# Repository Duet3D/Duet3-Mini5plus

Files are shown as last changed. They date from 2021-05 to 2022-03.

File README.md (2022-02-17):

# Duet3-Mini5+
The Duet 3 Mini 5+ balances value and performance, focused on small and medium size machines that do not need the high power output of the Duet 3 Mainboard 6HC. 

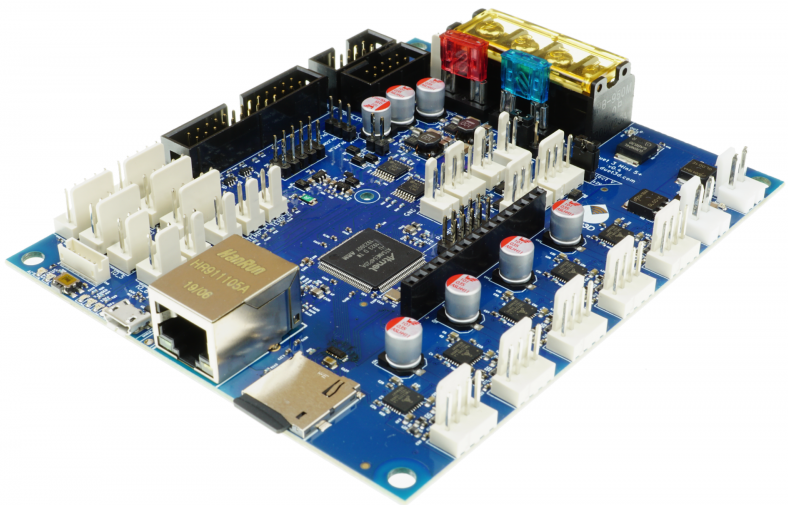
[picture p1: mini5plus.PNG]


Product page is here: https://www.duet3d.com/Duet3Mini5plus

Documentation is here: https://docs.duet3d.com/Duet3D_hardware/Duet_3_family/Duet_3_Mini_5+_Hardware_Overview

This repository also contains information in the Mini 2+ : a two driver expansion board for the Duet 3 mini 5+
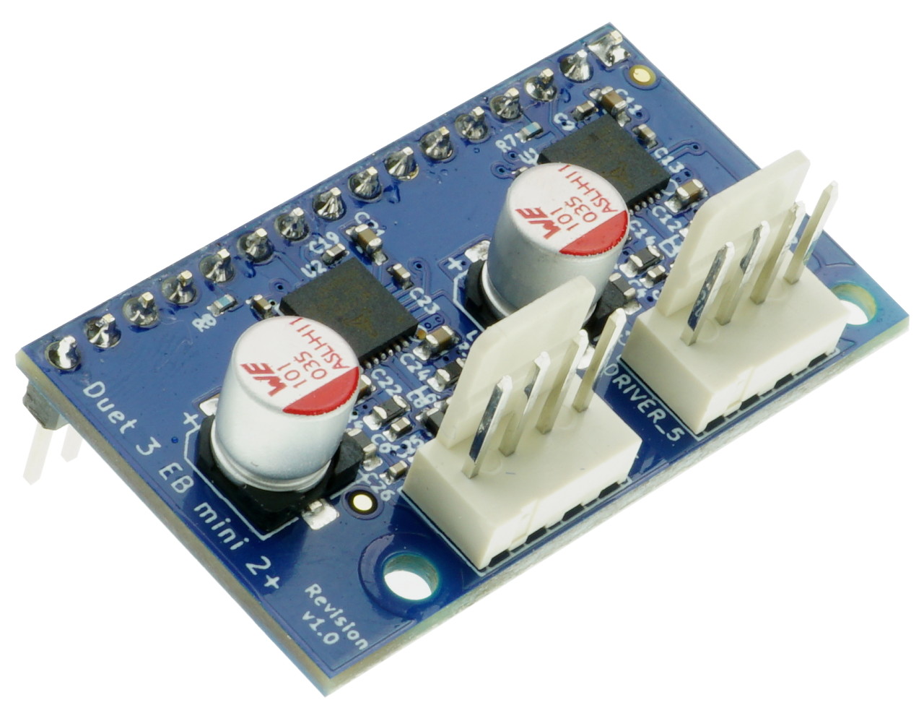
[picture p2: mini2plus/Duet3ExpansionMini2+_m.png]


Product page is here: https://www.duet3d.com/Duet3ExpansionMini2plus

Documentation is here: https://docs.duet3d.com/Duet3D_hardware/Duet_3_family/Duet_3_Expansion_Mini_2+

As always please discuss this on the Duet3d forum: https://forum.duet3d.com/

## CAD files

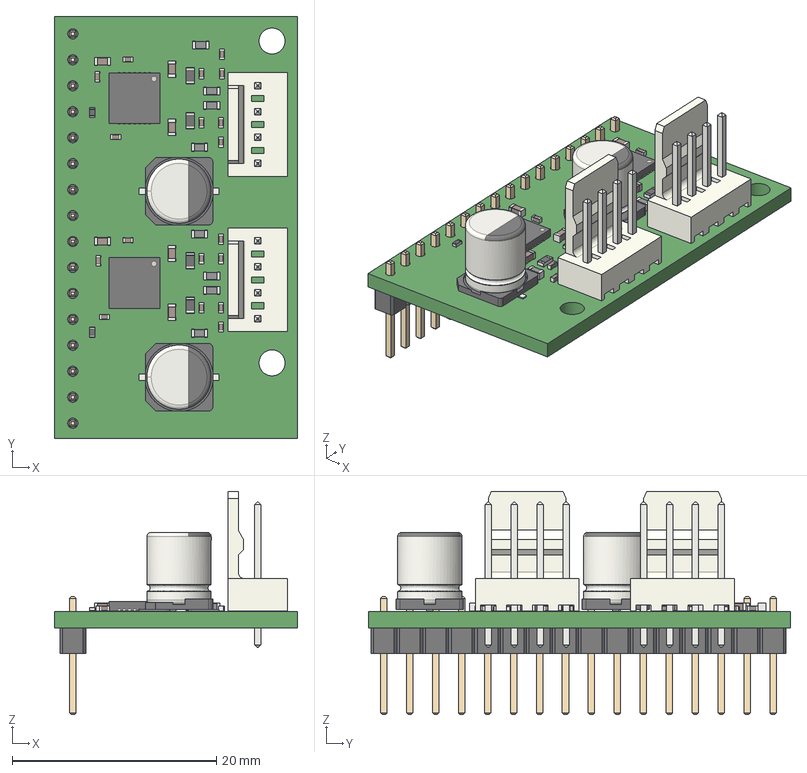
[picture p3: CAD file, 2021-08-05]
mini2plus/v1.0/Duet3_Exp_2plus.step
23.8 x 41.3 x 21.8 mm

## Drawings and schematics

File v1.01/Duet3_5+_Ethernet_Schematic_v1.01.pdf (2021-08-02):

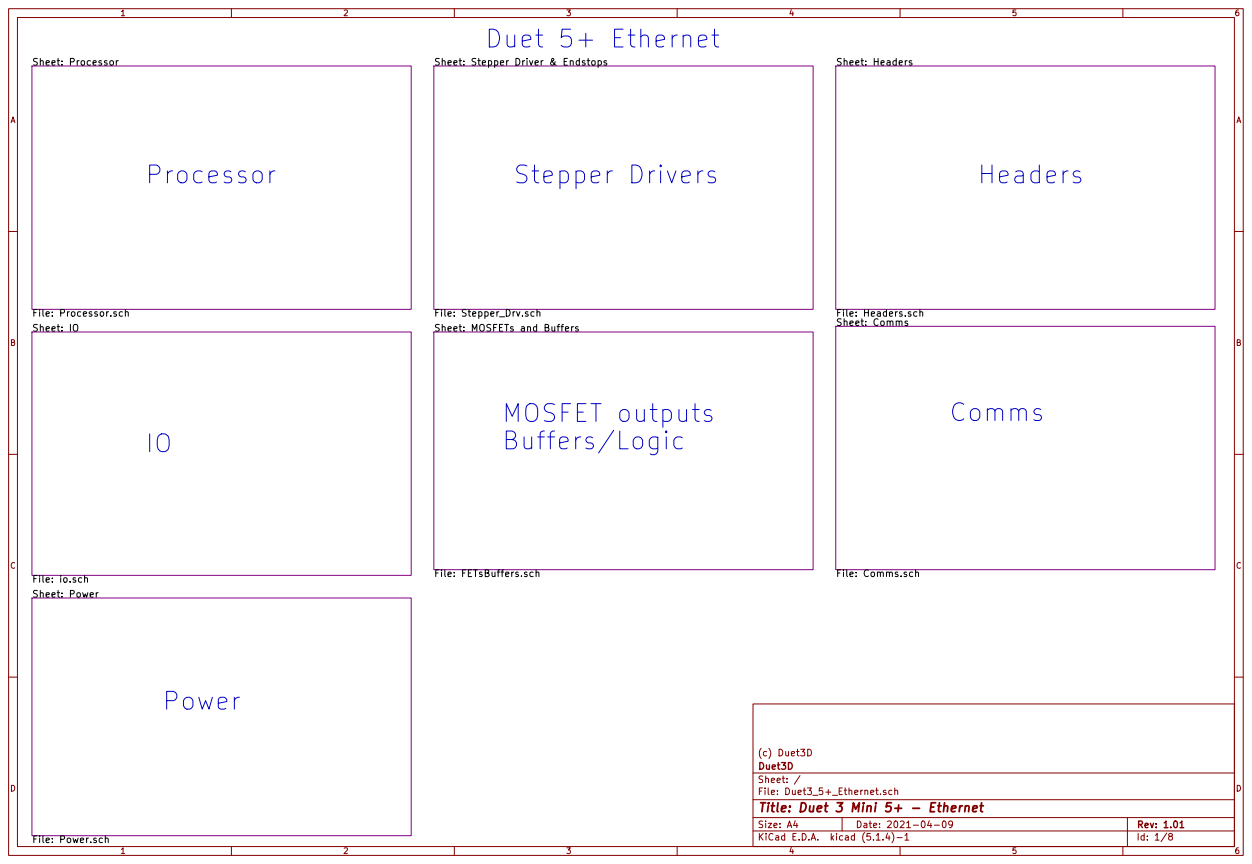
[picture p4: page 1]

Sheet: Headers File: Headers.sch Sheet: Power File: Power.sch

Sheet: Stepper Driver & Endstops

Id: 1/8 Title: Duet 3 Mini 5+ - Ethernet

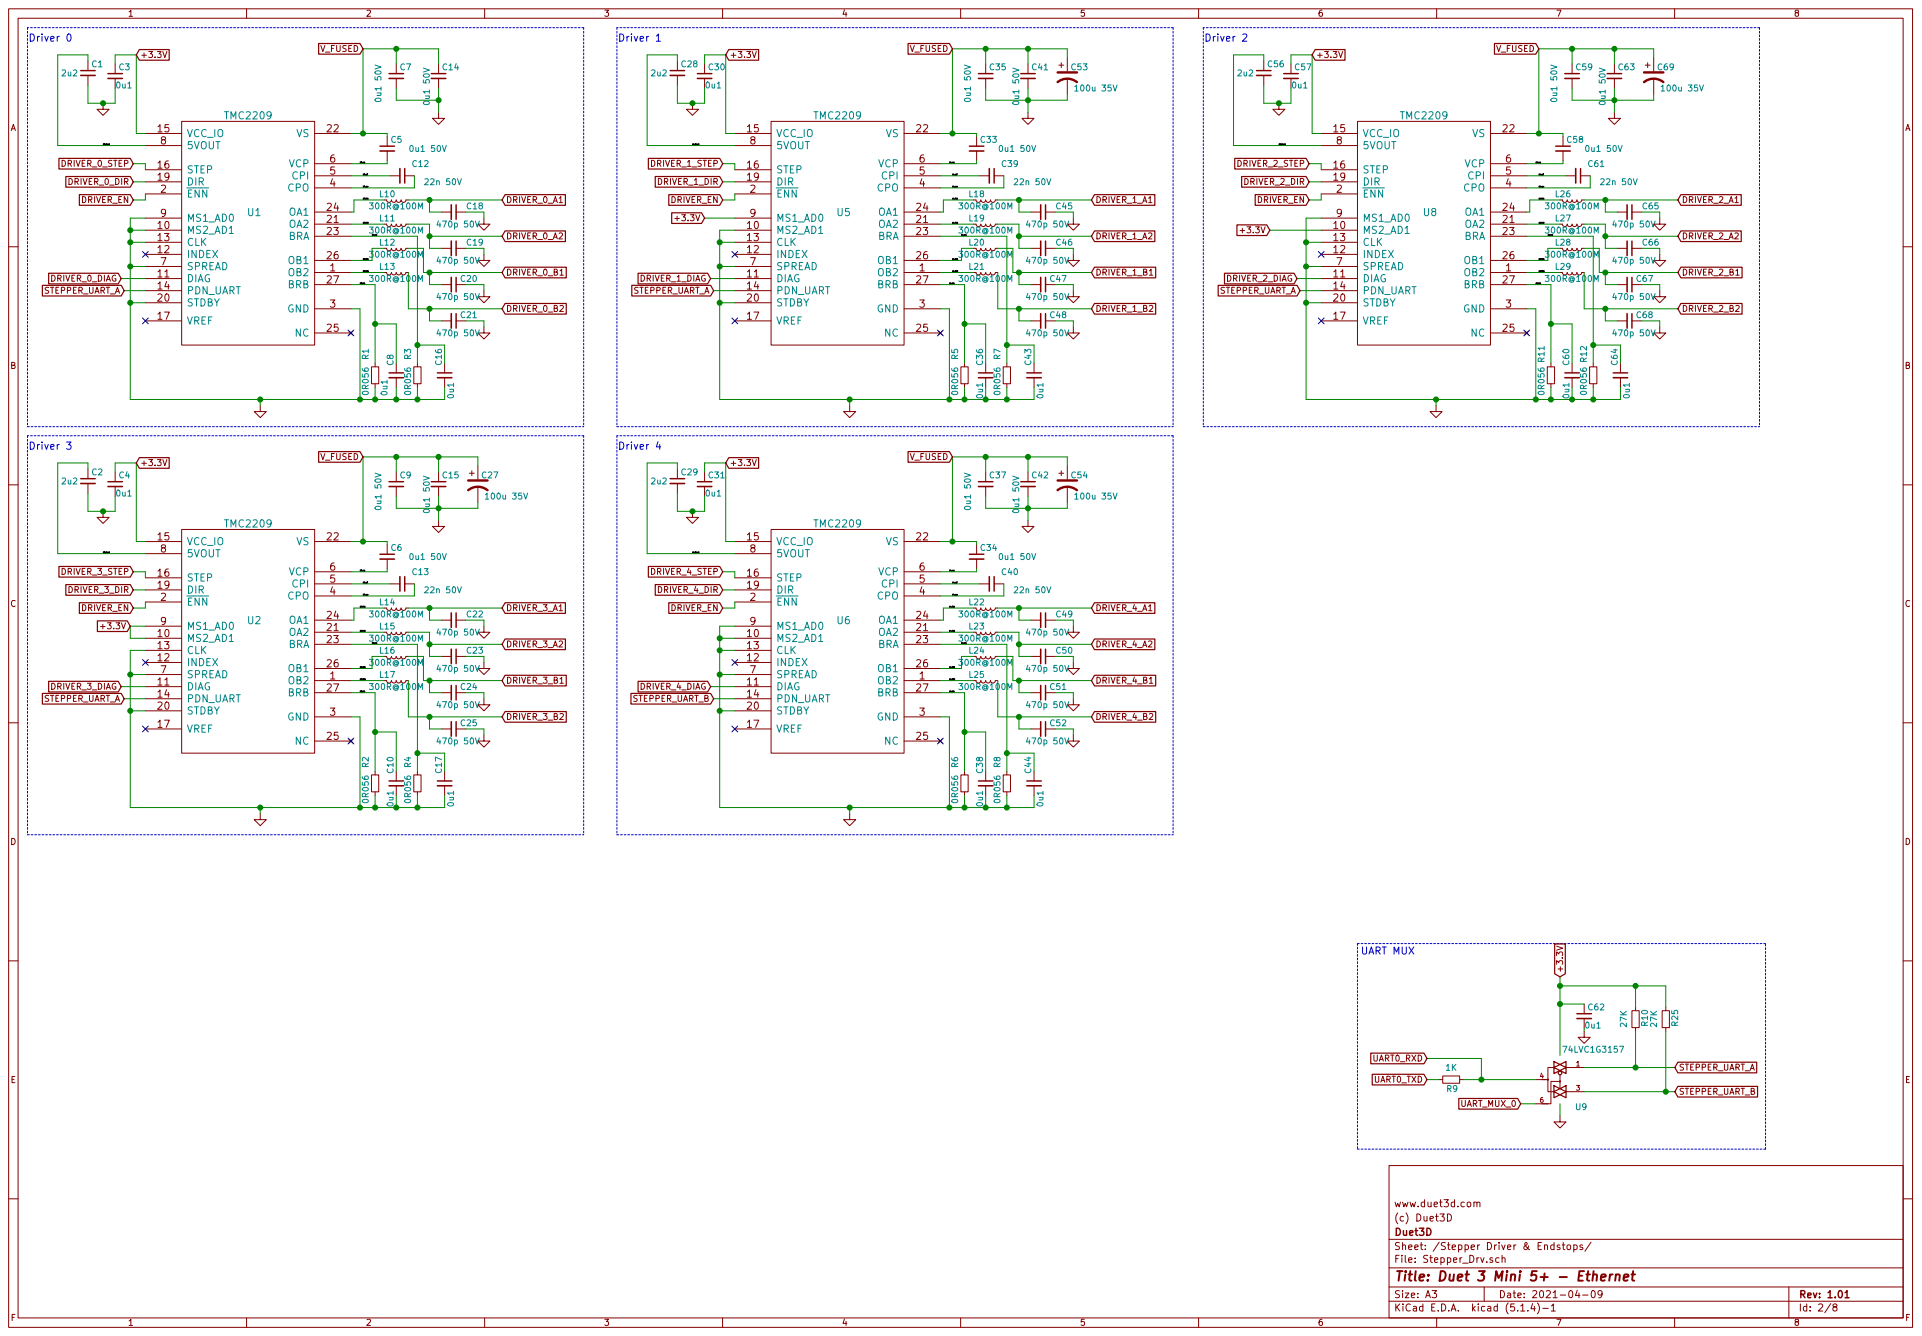
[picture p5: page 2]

www.duet3d.com
(c) Duet3D
Sheet: /Stepper Driver & Endstops/ Duet3D

File: Stepper_Drv.sch
Id: 2/8 Title: Duet 3 Mini 5+ - Ethernet

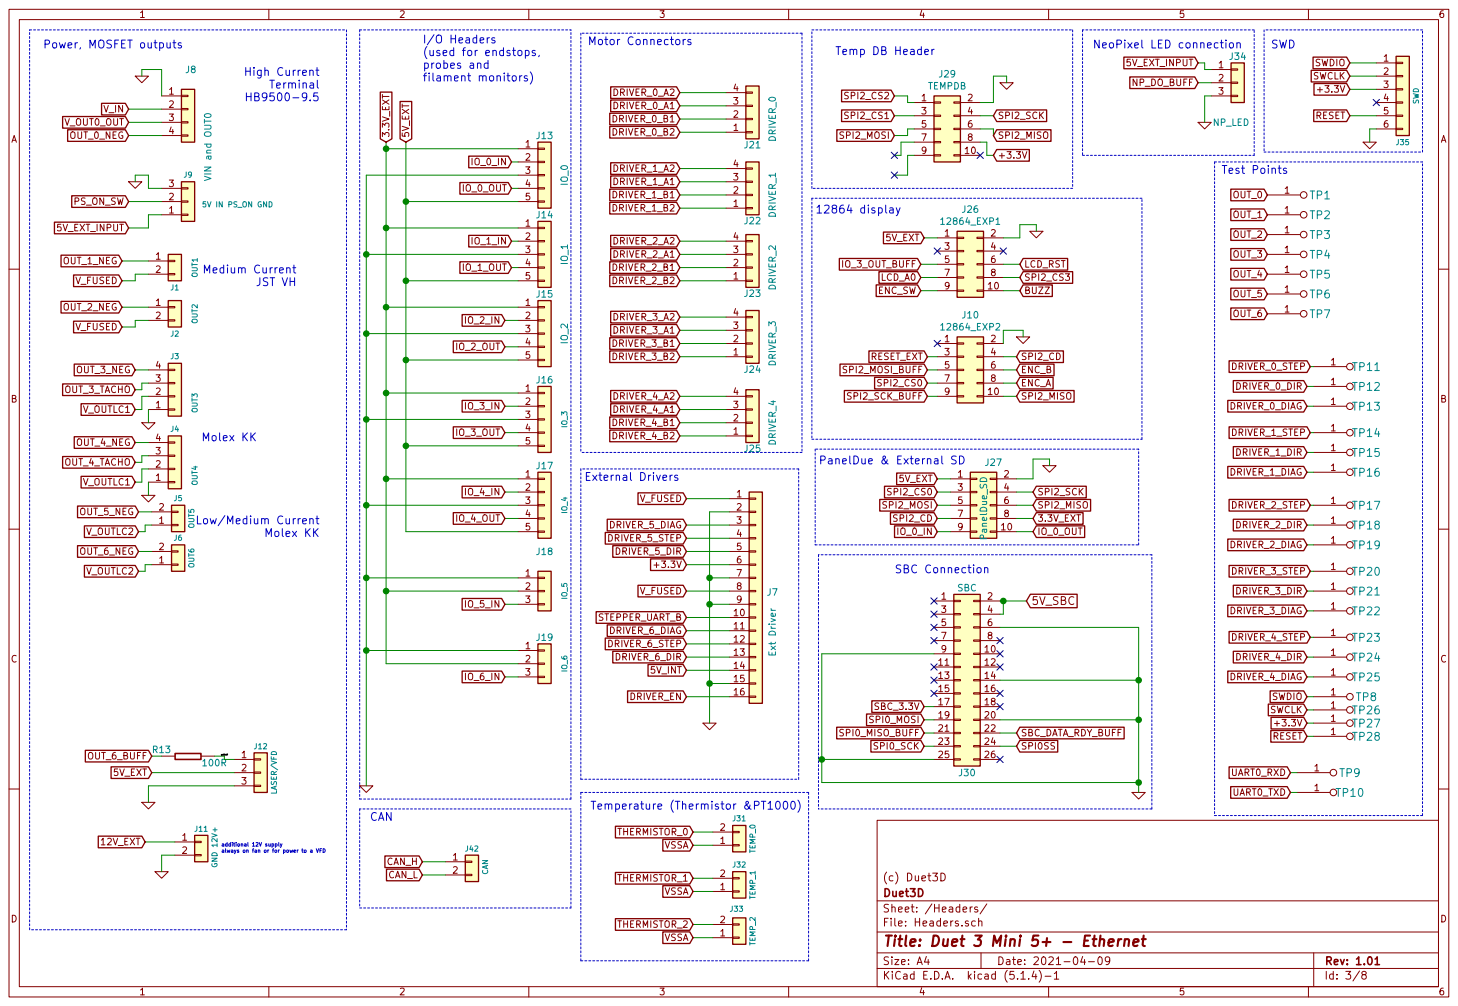
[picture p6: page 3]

High Current Terminal HB9500-9.5 Power, MOSFET outputs

4 IO_0_OUT 5

Low/Medium Current Molex KK

(c) Duet3D
Id: 3/8 Title: Duet 3 Mini 5+ - Ethernet File: Headers.sch Sheet: /Headers/ Duet3D

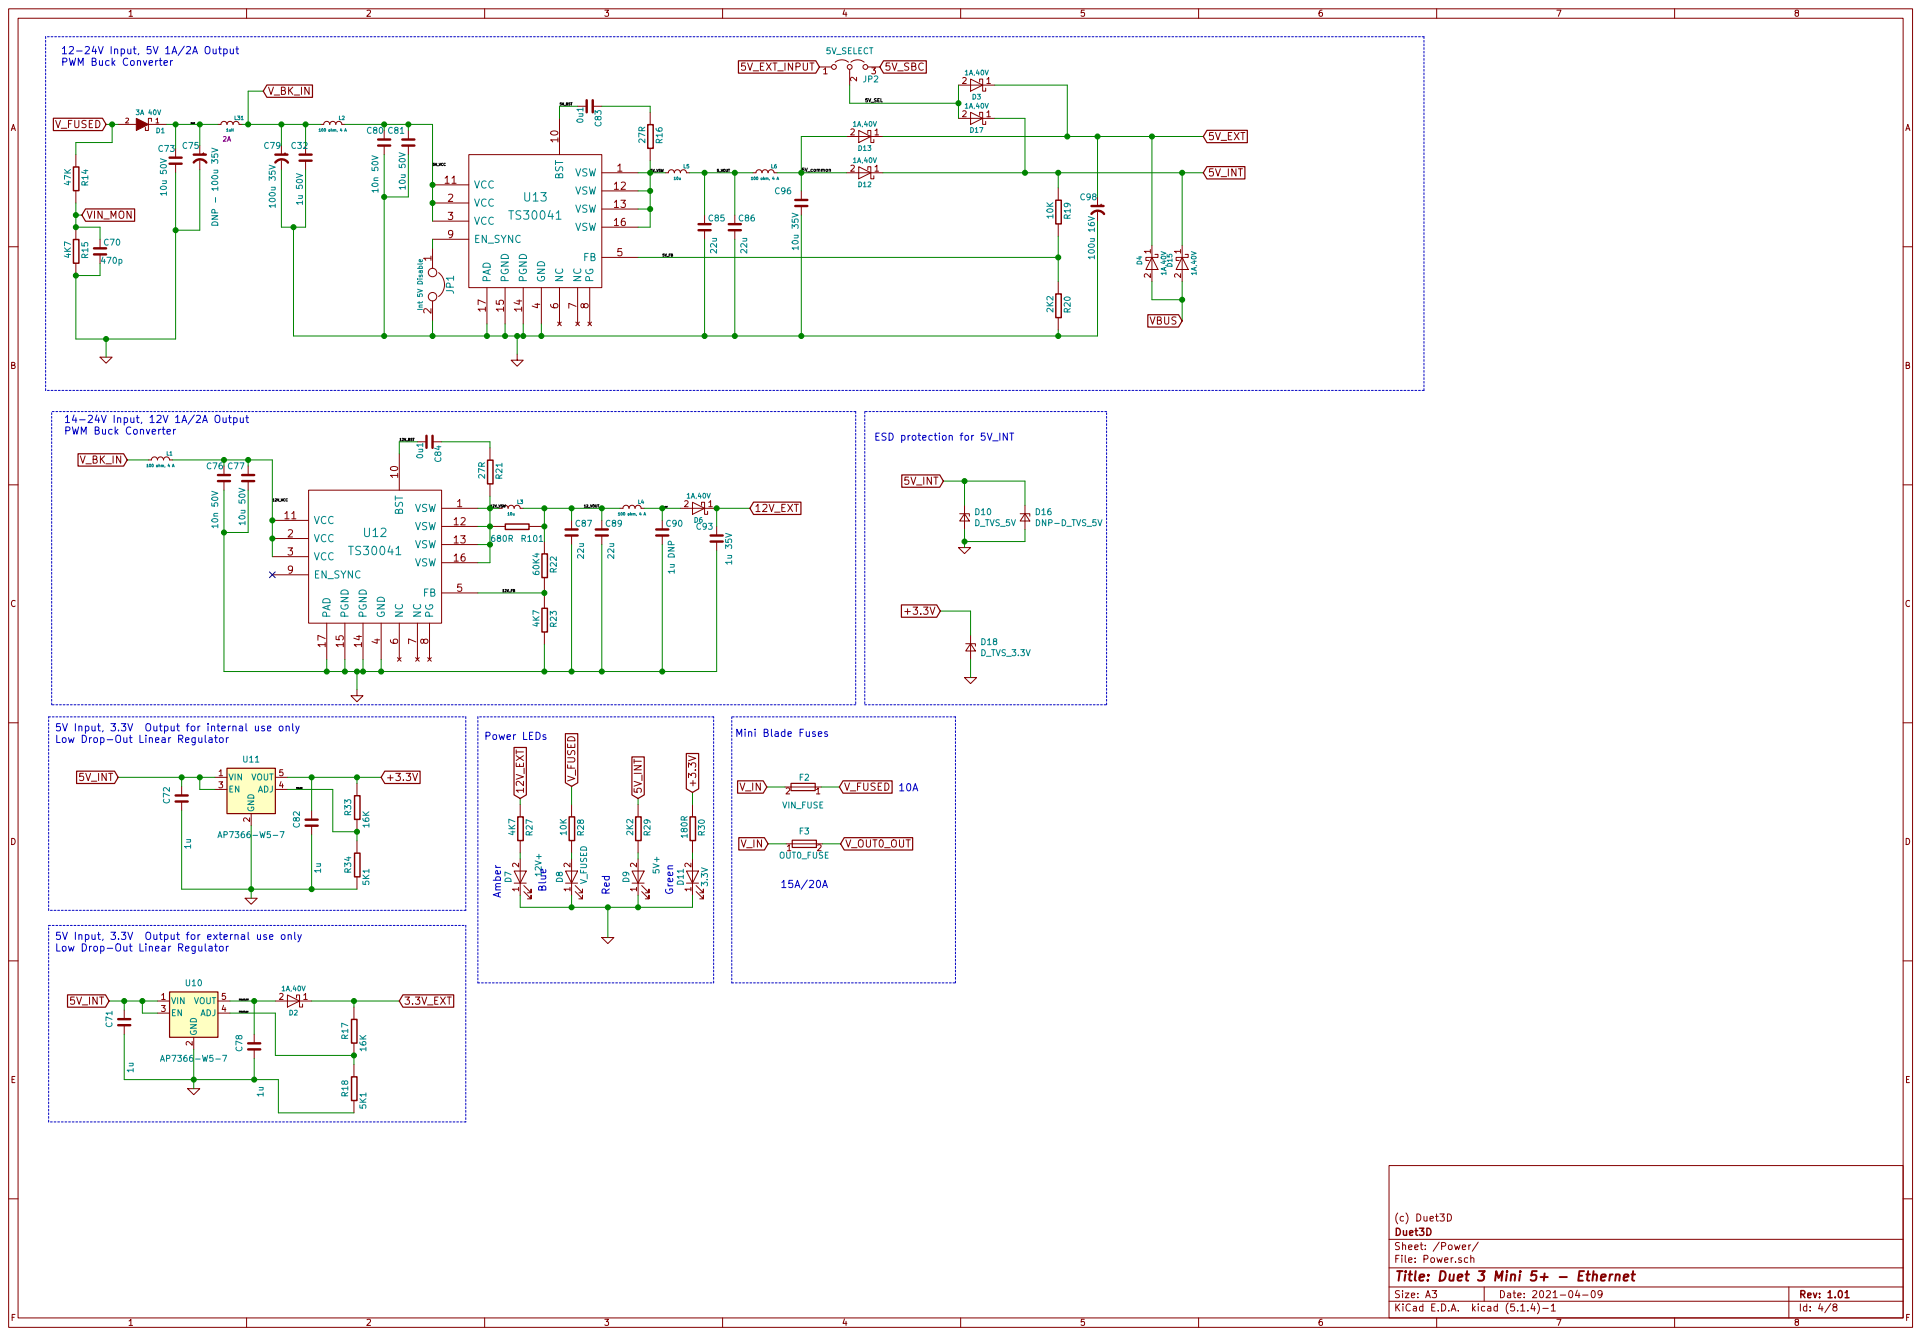
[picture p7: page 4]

5V Input, 3.3V Output for internal use only

5V Input, 3.3V Output for external use only

(c) Duet3D
Id: 4/8 Title: Duet 3 Mini 5+ - Ethernet File: Power.sch Sheet: /Power/ Duet3D

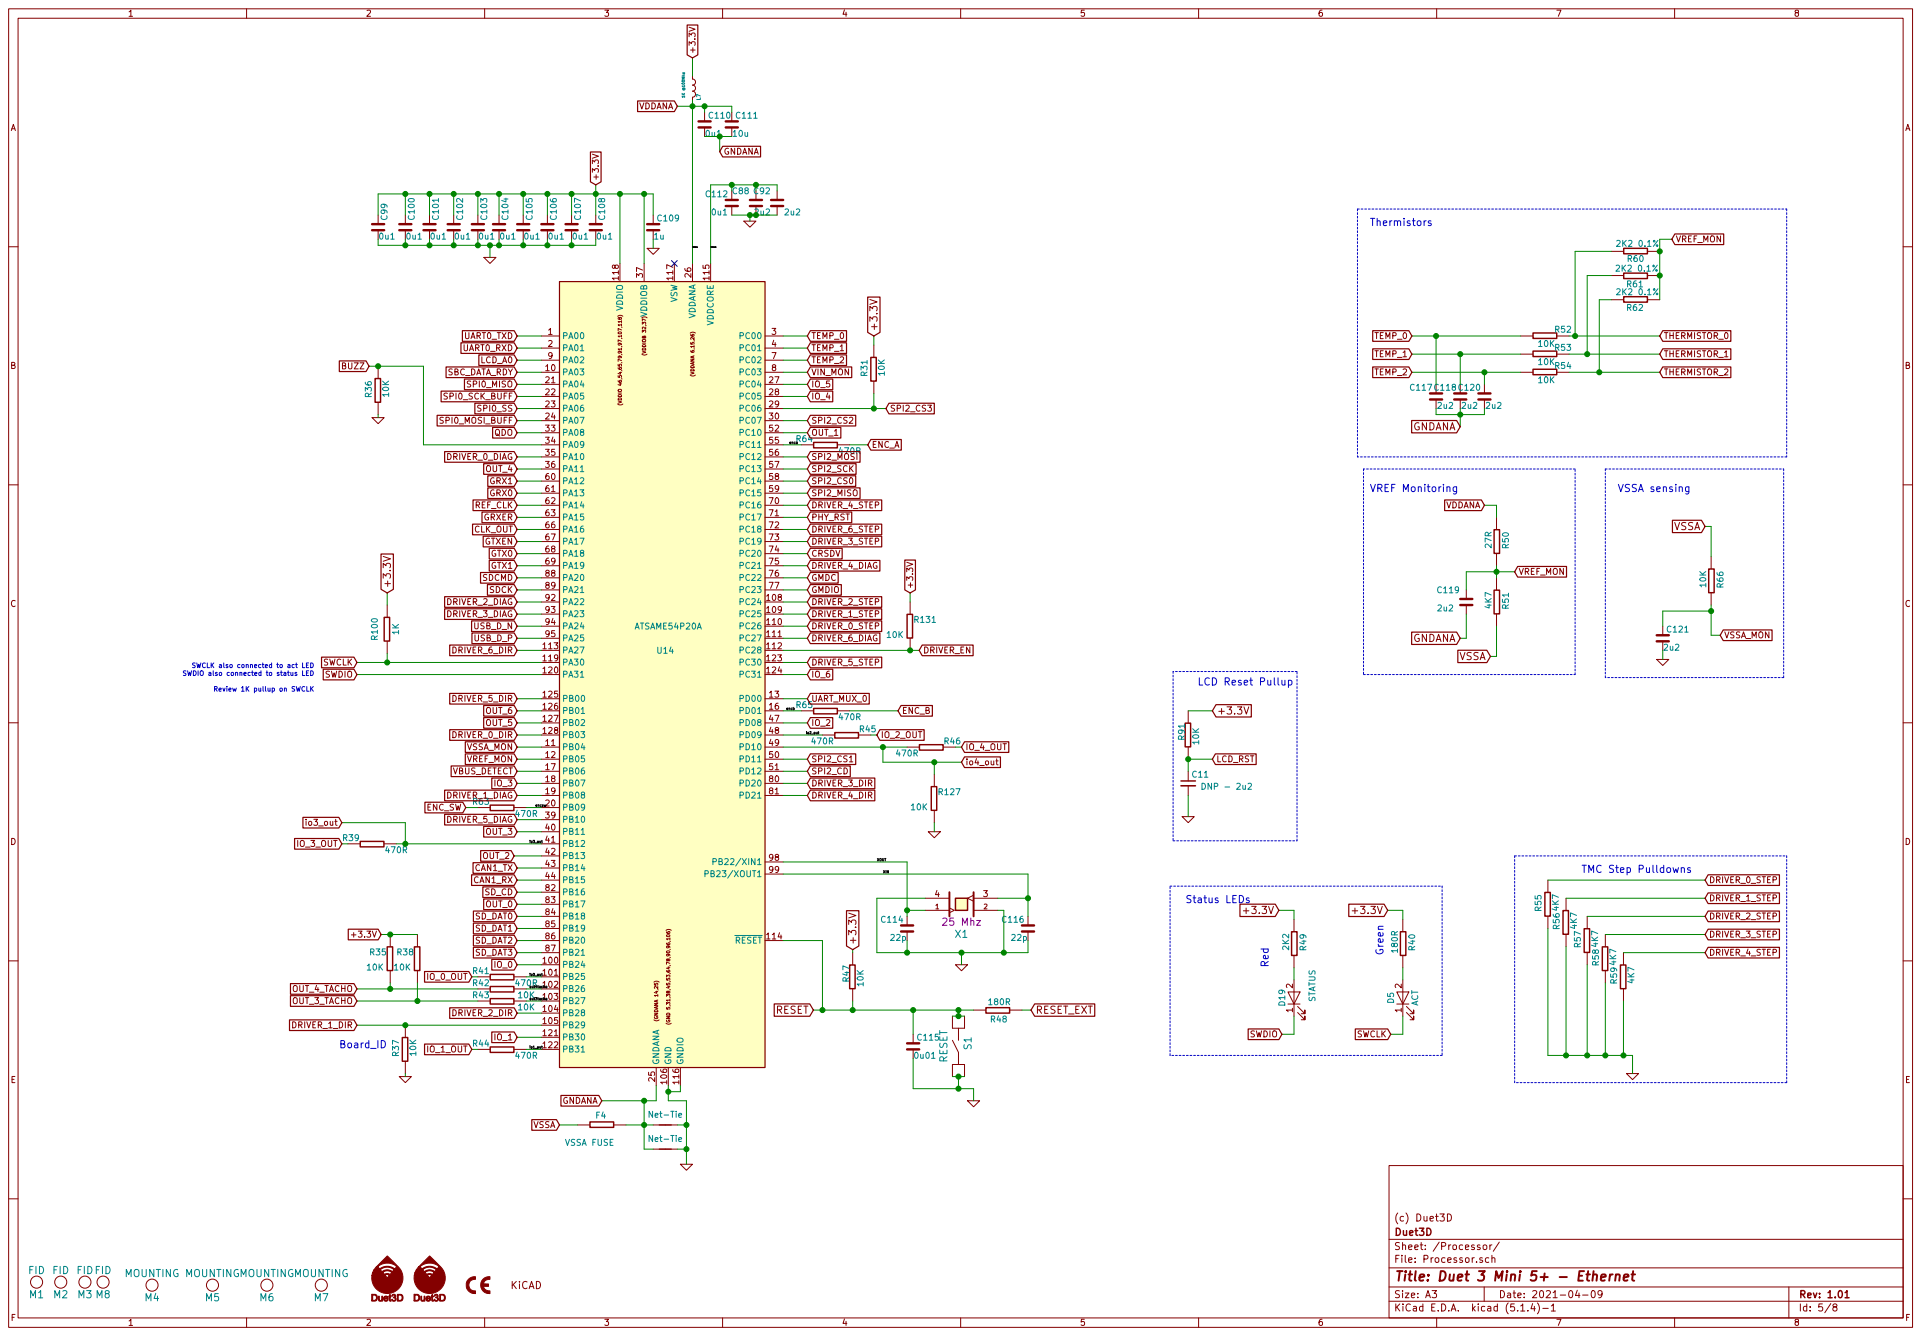
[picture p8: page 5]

Thermistors LCD Reset Pullup

SWCLK also connected to act LED
SWDIO also connected to status LED

Review 1K pullup on SWCLK

TMC Step Pulldowns Green Red

Id: 5/8 Title: Duet 3 Mini 5+ - Ethernet File: Processor.sch Sheet: /Processor/ Duet3D

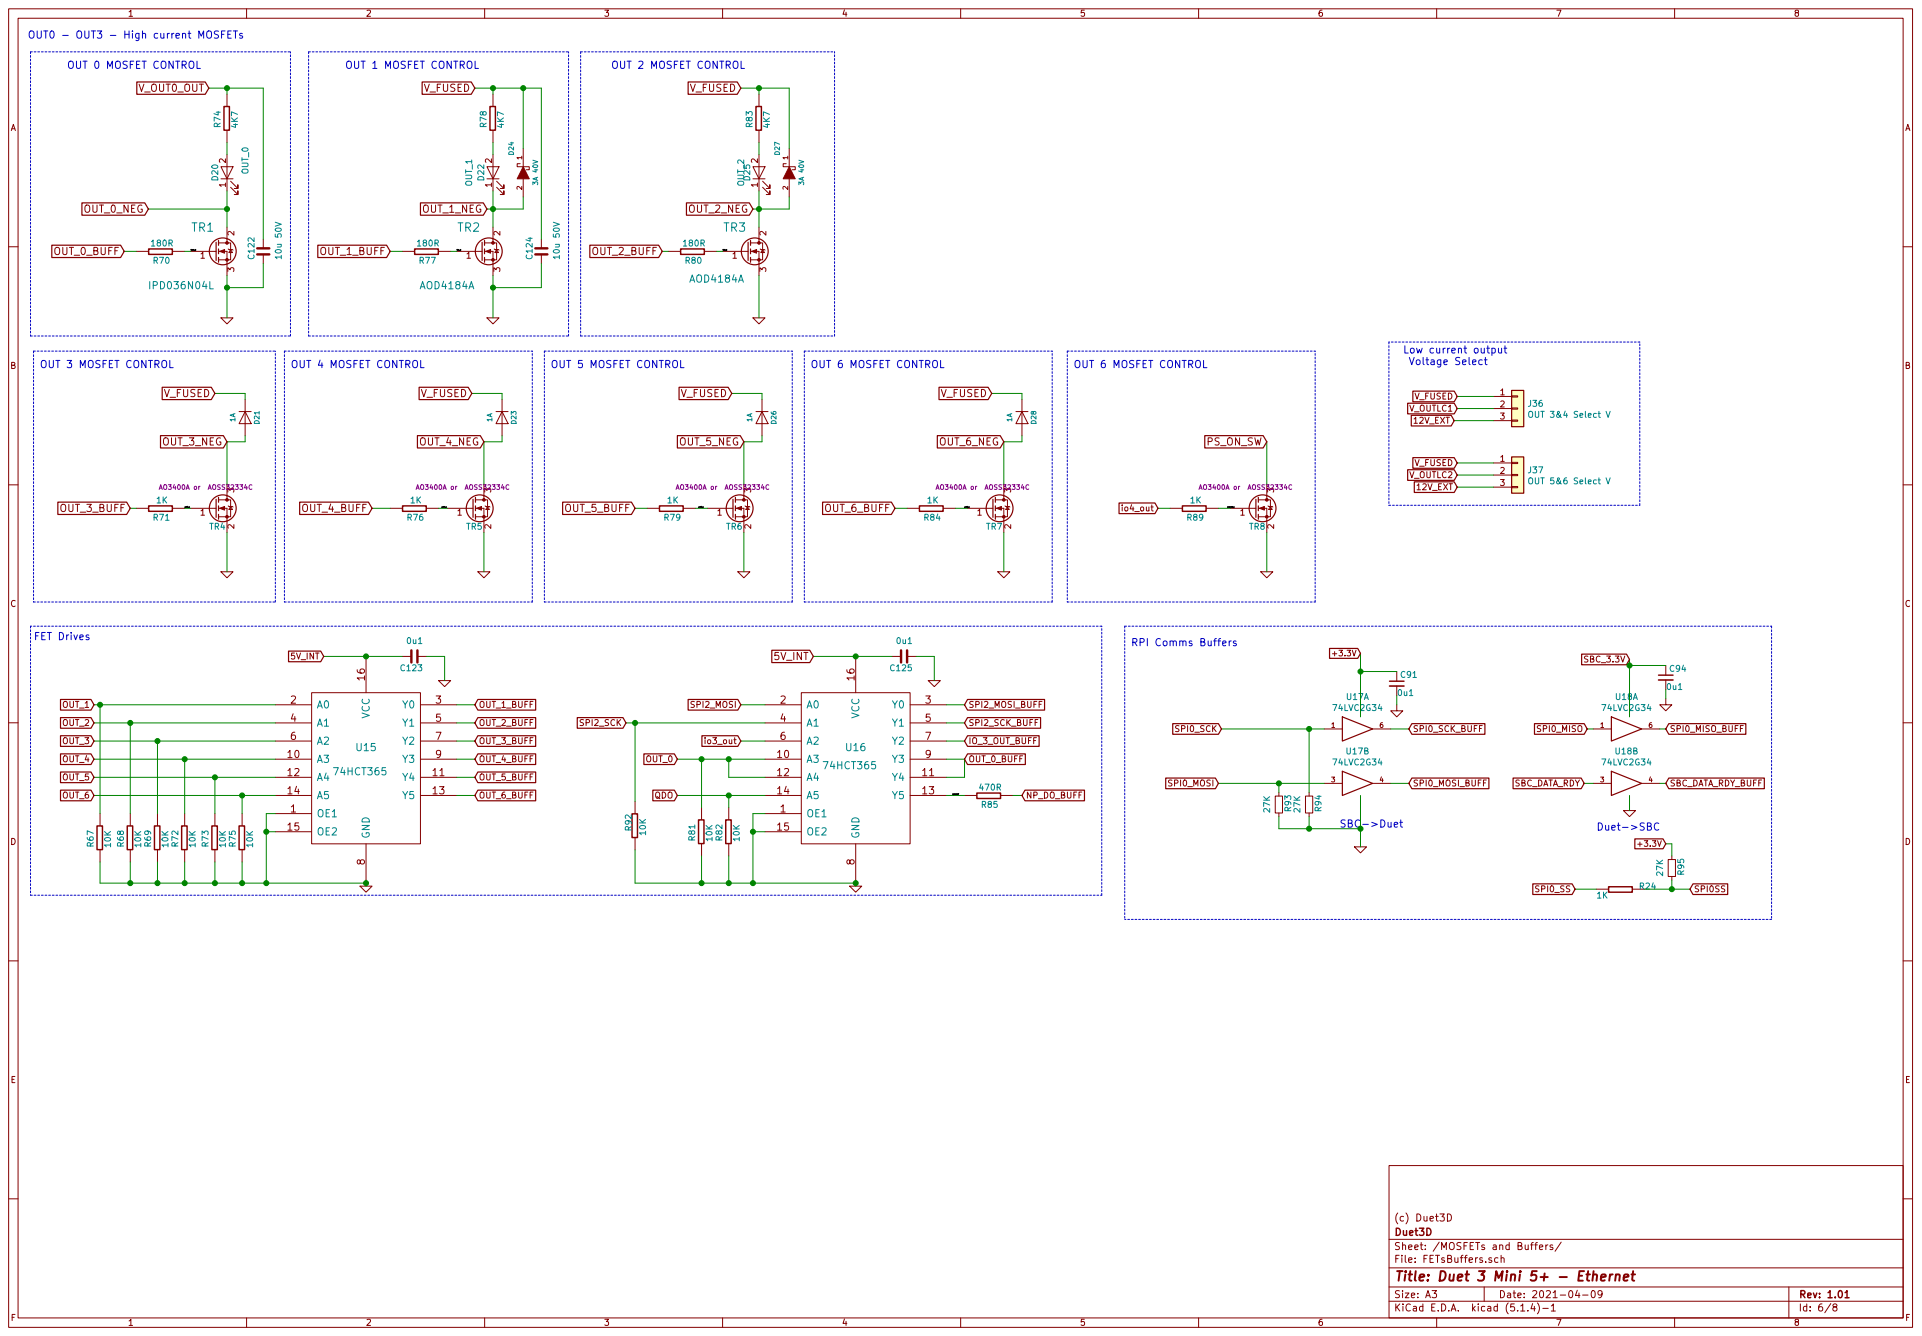
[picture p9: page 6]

OUT0 - OUT3 - High current MOSFETs FET Drives OUT 3 MOSFET CONTROL

(c) Duet3D
Id: 6/8 Title: Duet 3 Mini 5+ - Ethernet File: FETsBuffers.sch Sheet: /MOSFETs and Buffers/ Duet3D

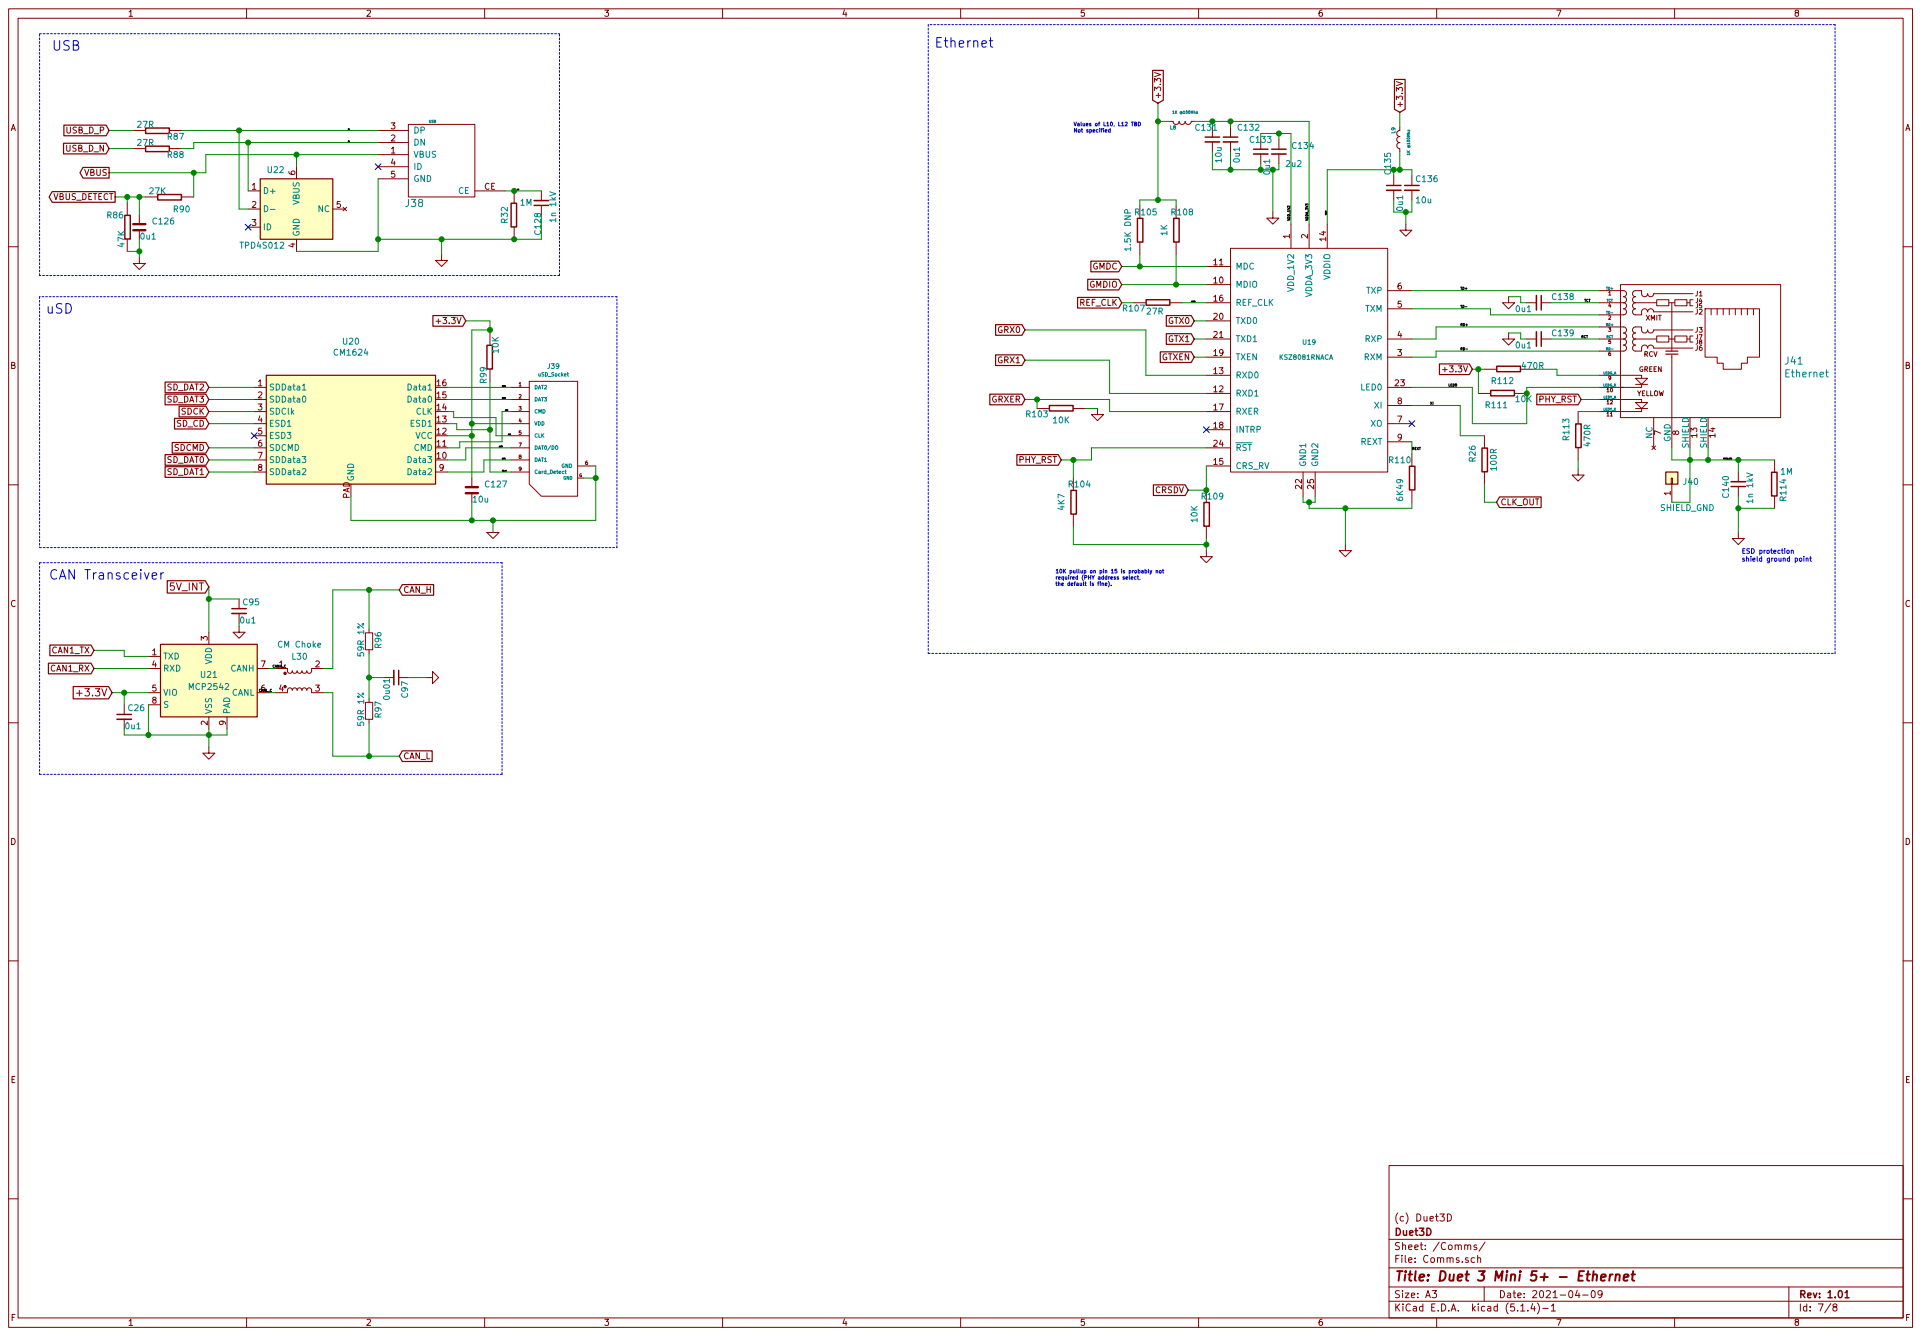
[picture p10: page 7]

1 MDIO 10 MDC 11 RXD1 12 RXD0 13 VDDIO 14 CRS_RV 15 REF_CLK 16 RXER 17

shield ground point uSD

the default is fine). CAN Transceiver

3 RXD 4 VIO 5 CANL 6 CANH 7 S

(c) Duet3D
Id: 7/8 Title: Duet 3 Mini 5+ - Ethernet File: Comms.sch Sheet: /Comms/ Duet3D

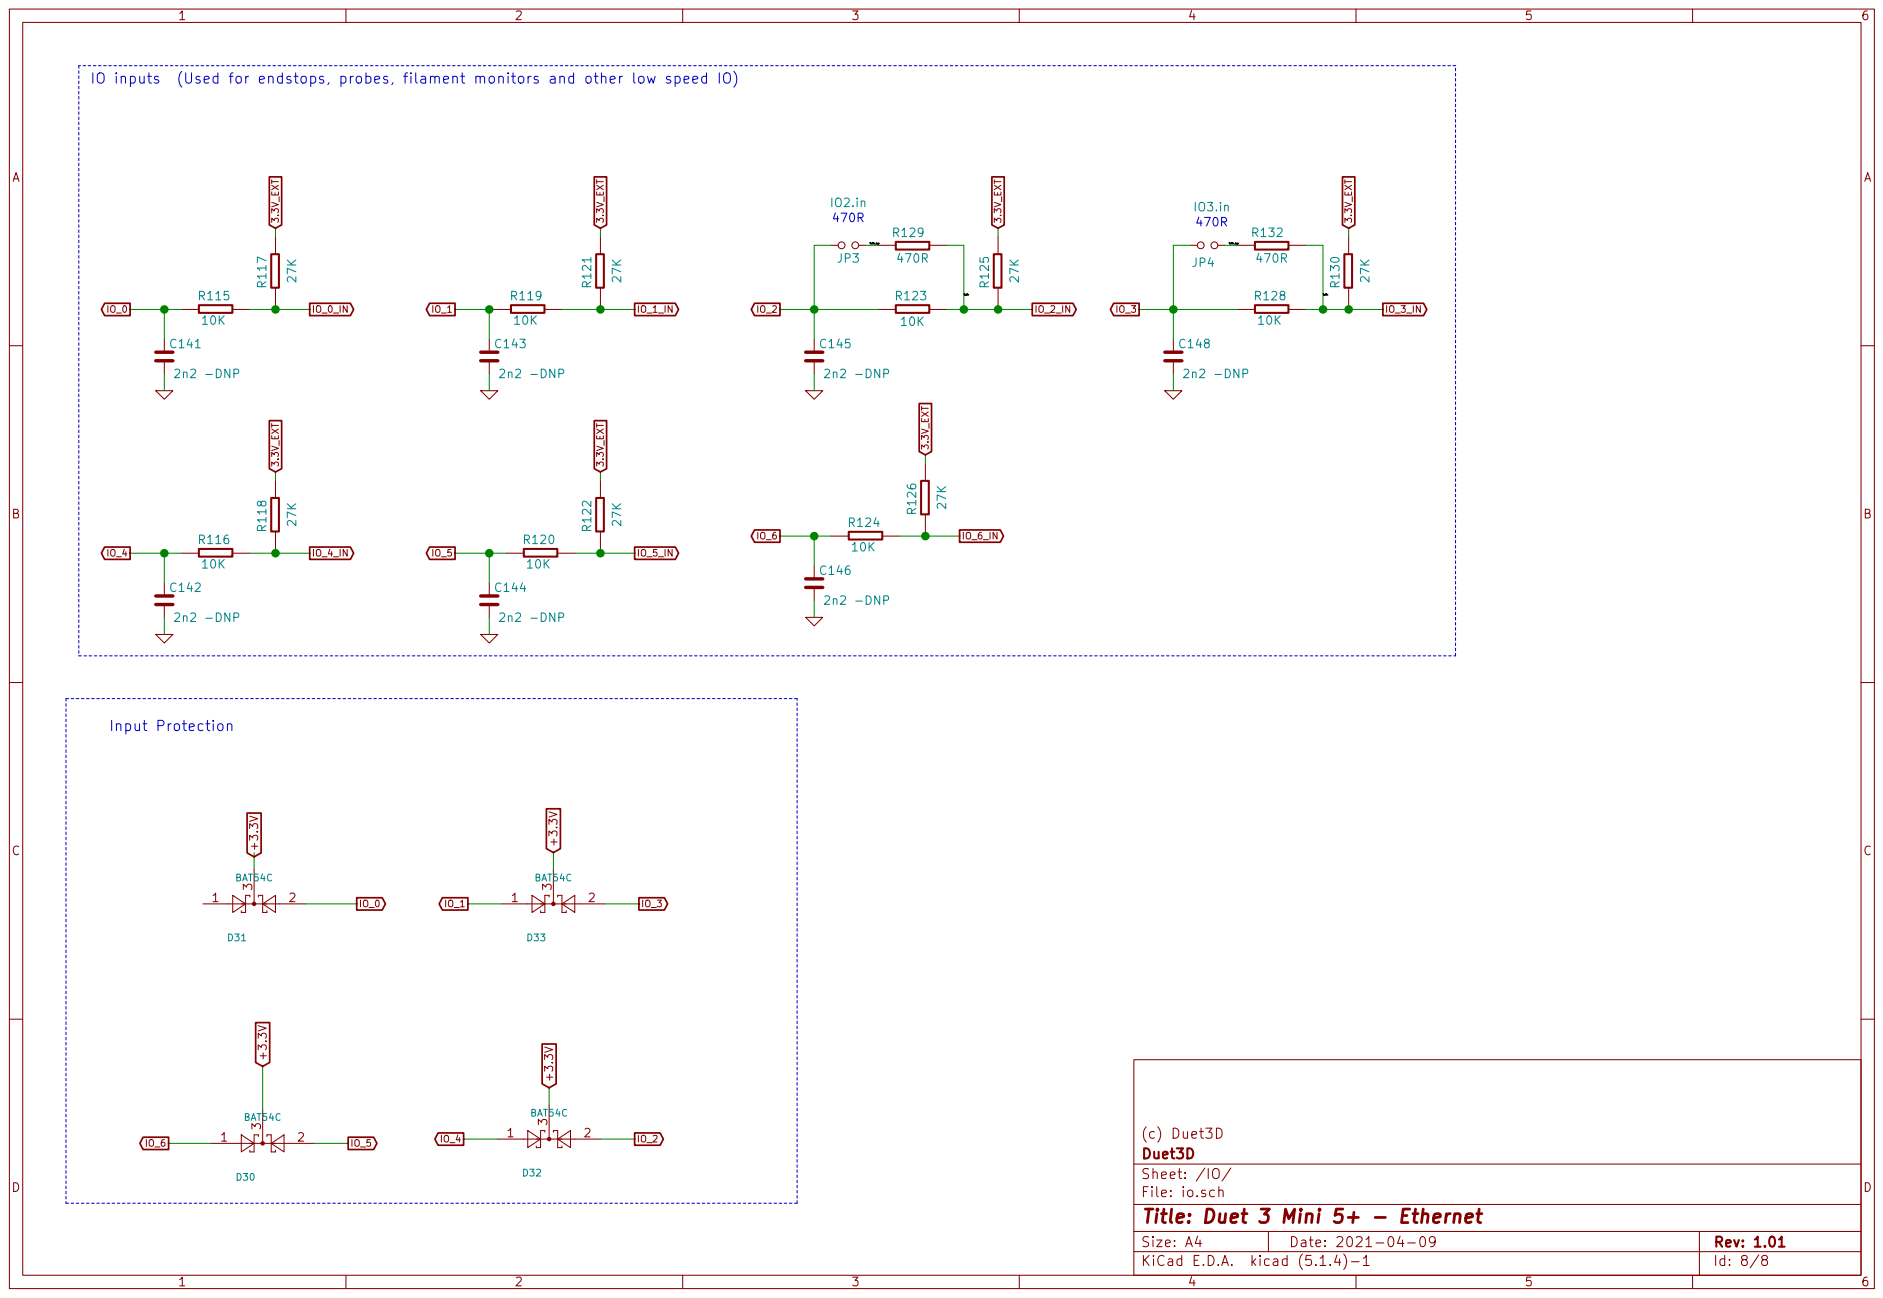
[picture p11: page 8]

IO inputs (Used for endstops, probes, filament monitors and other low speed IO)

Id: 8/8 Title: Duet 3 Mini 5+ - Ethernet File: io.sch Sheet: /IO/ Duet3D

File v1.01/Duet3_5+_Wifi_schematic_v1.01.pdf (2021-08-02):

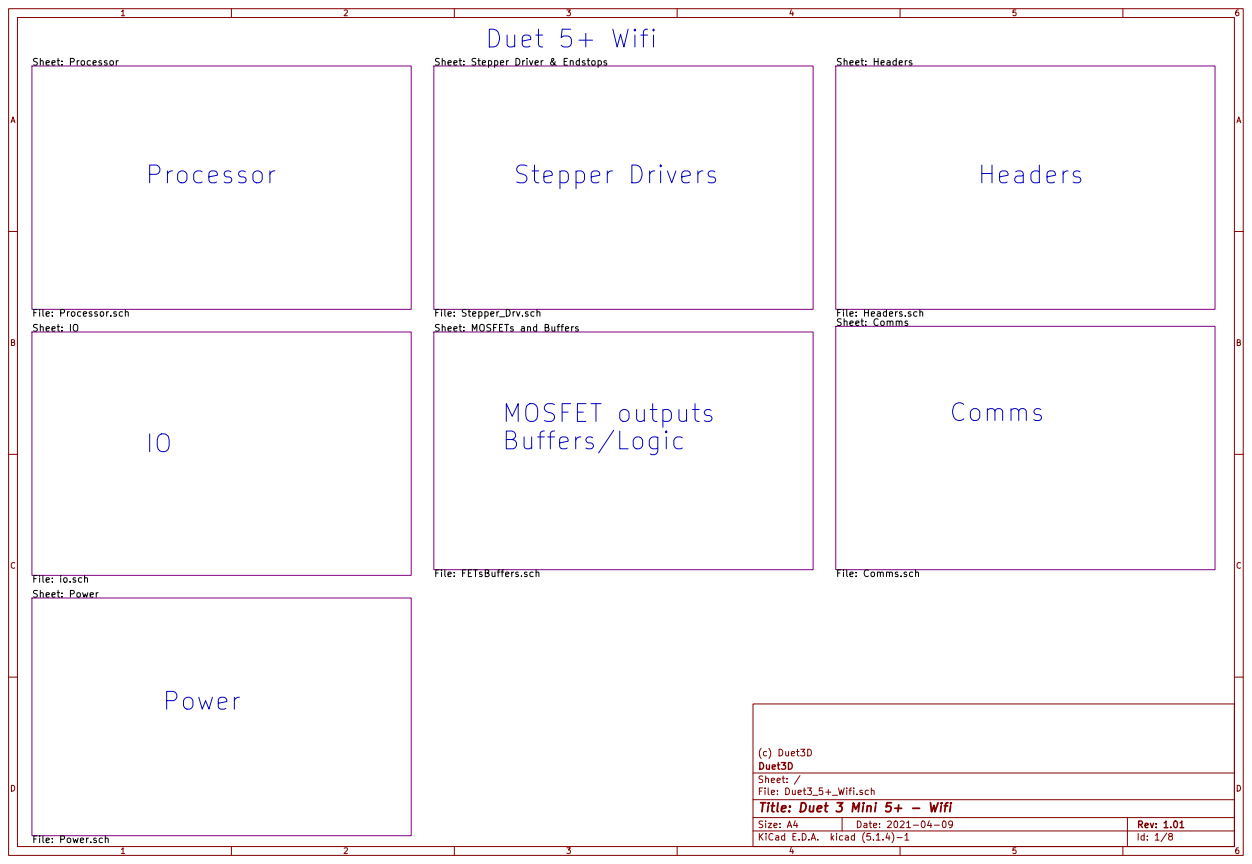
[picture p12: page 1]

Sheet: Headers File: Headers.sch Sheet: Power File: Power.sch

Sheet: Stepper Driver & Endstops

Id: 1/8 Title: Duet 3 Mini 5+ - Wifi

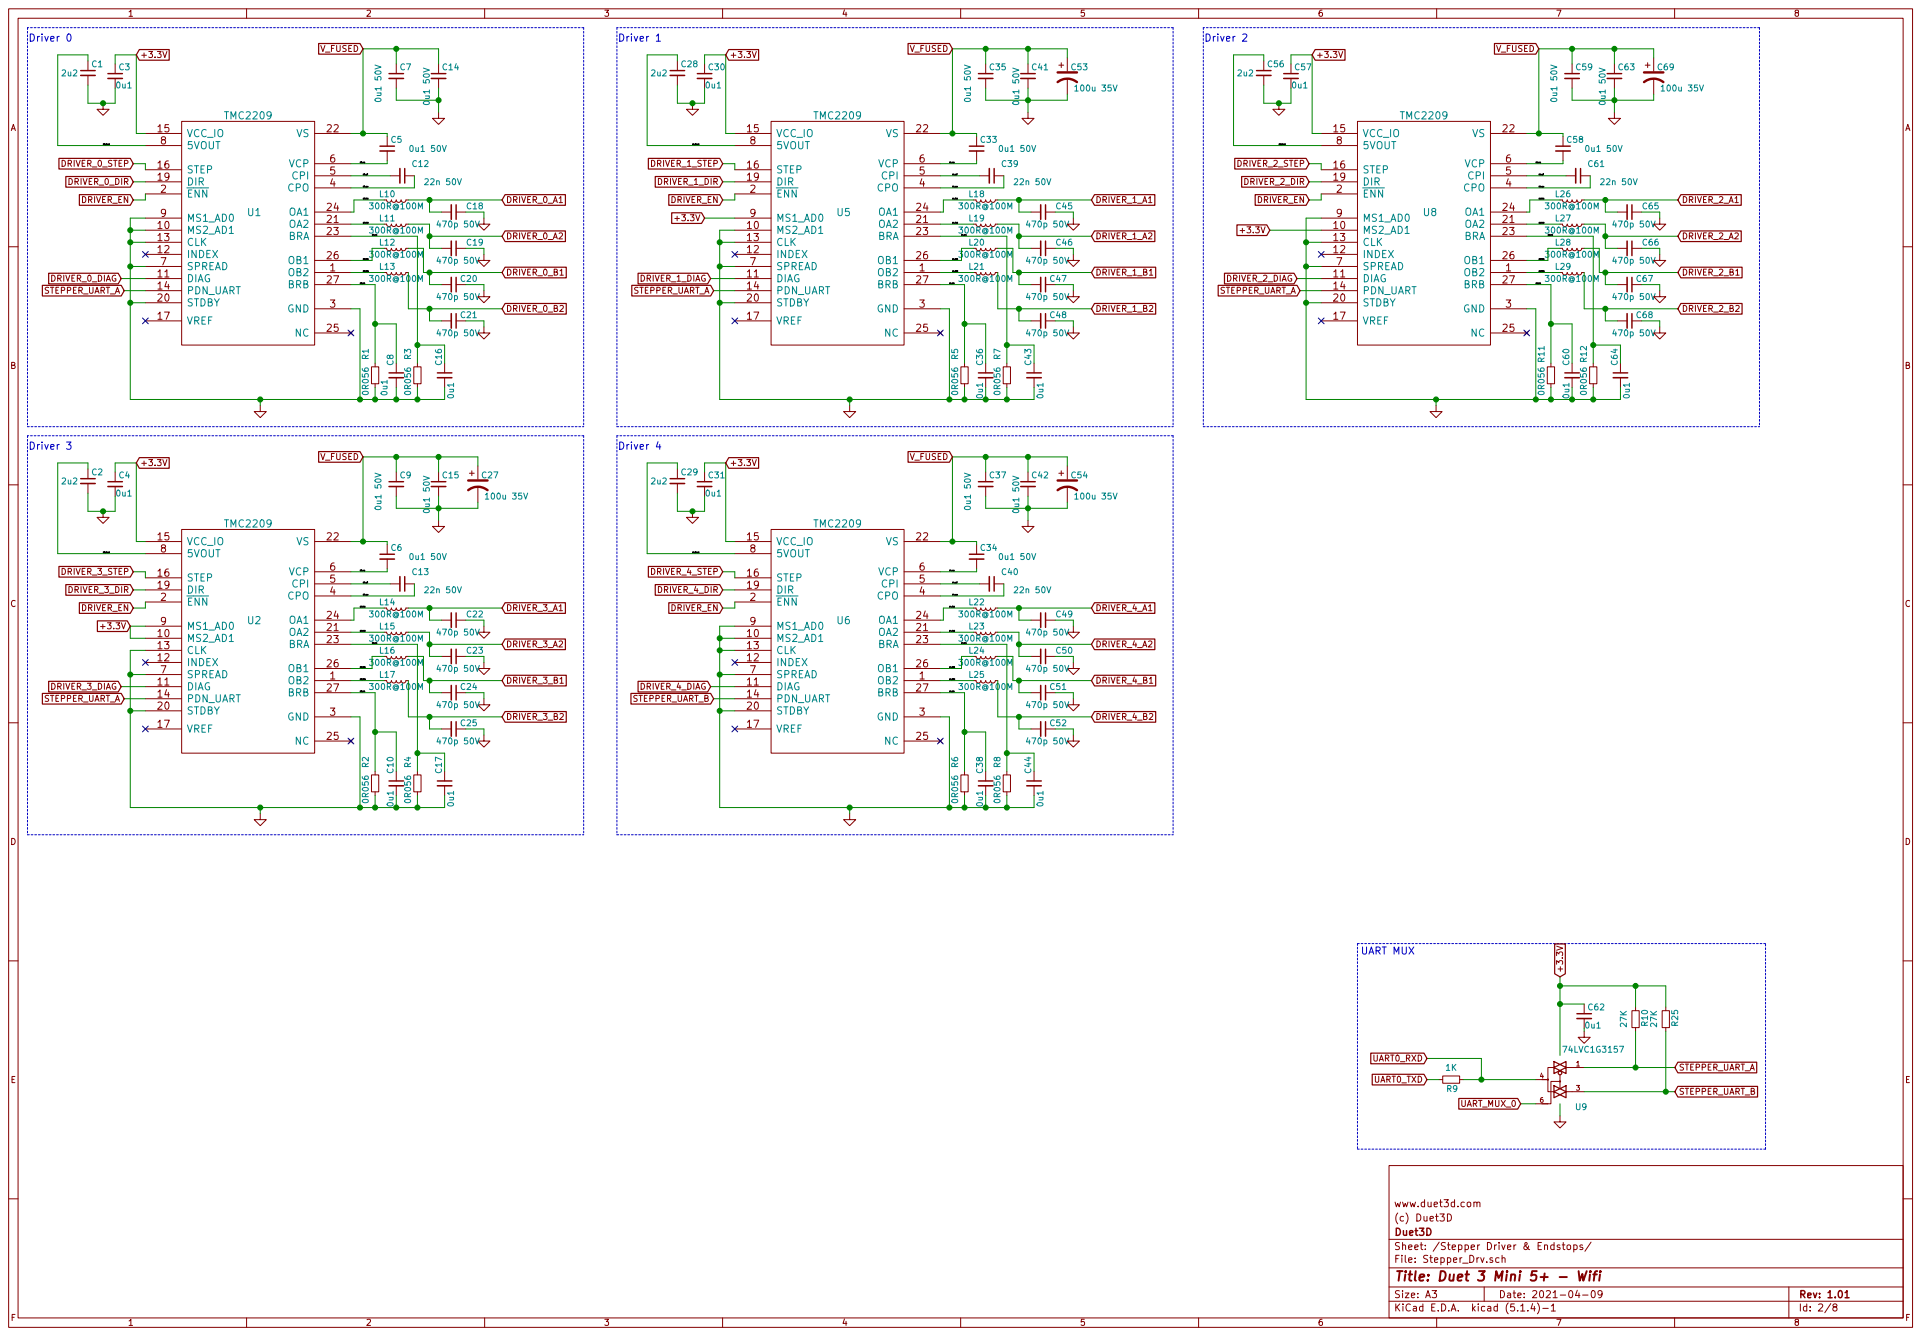
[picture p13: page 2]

(c) Duet3D
Sheet: /Stepper Driver & Endstops/ Duet3D

File: Stepper_Drv.sch
Id: 2/8 Title: Duet 3 Mini 5+ - Wifi

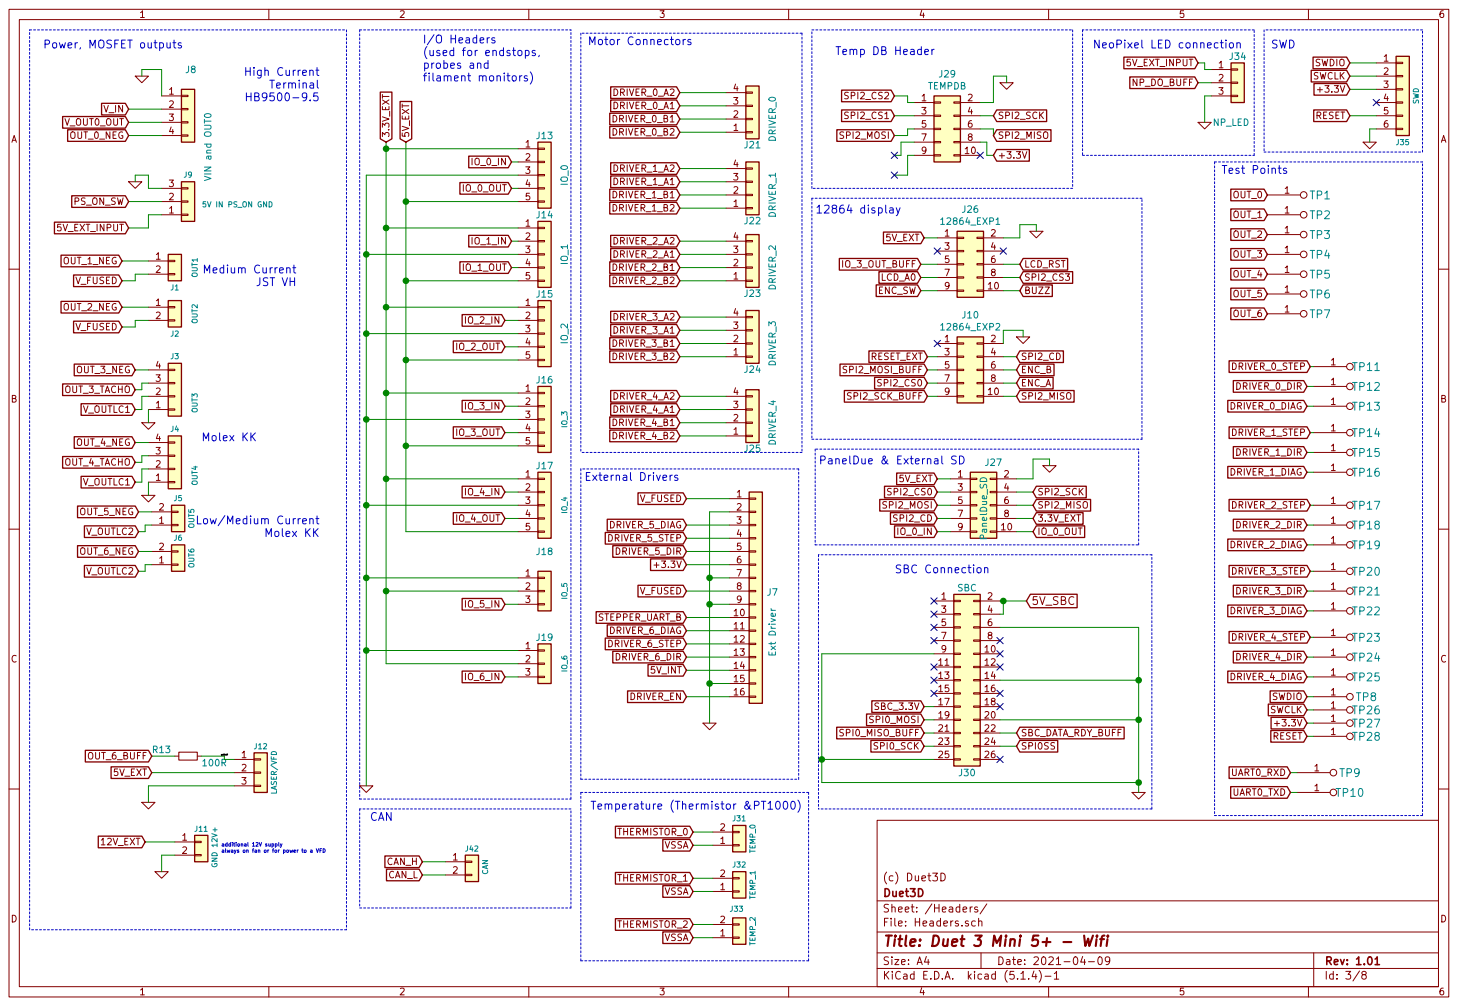
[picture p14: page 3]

Test Points Motor Connectors

4 IO_0_OUT 5

Low/Medium Current Molex KK

(c) Duet3D
Id: 3/8 Title: Duet 3 Mini 5+ - Wifi File: Headers.sch Sheet: /Headers/ Duet3D

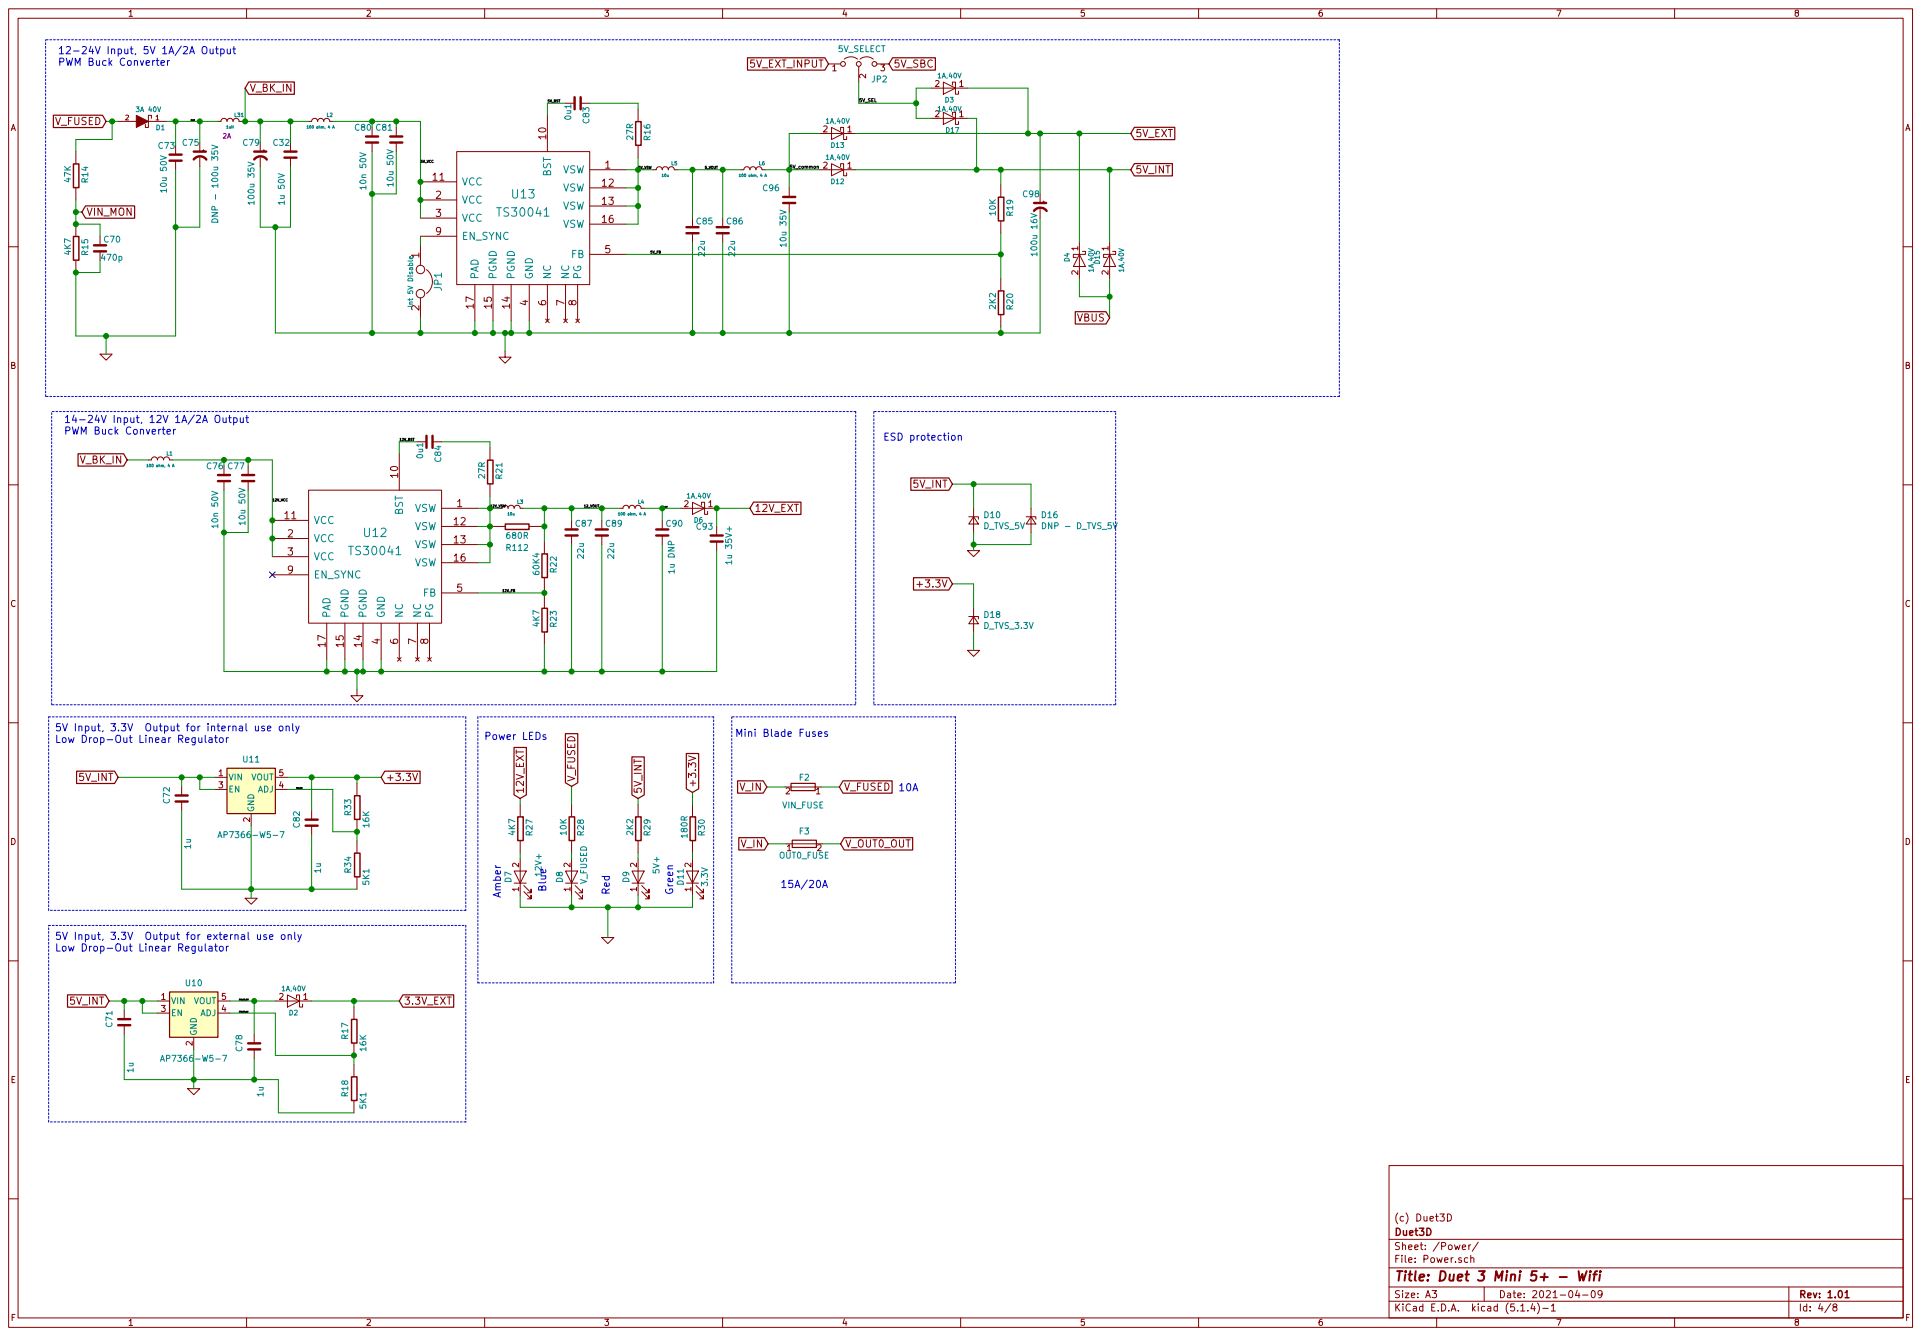
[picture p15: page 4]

5V Input, 3.3V Output for internal use only

5V Input, 3.3V Output for external use only

(c) Duet3D
Id: 4/8 Title: Duet 3 Mini 5+ - Wifi File: Power.sch Sheet: /Power/ Duet3D


SWCLK also connected to act LED
SWDIO also connected to status LED

(c) Duet3D
Id: 5/8 Title: Duet 3 Mini 5+ - Wifi File: Processor.sch Sheet: /Processor/ Duet3D


OUT0 - OUT3 - High current MOSFETs FET Drives OUT 3 MOSFET CONTROL

(c) Duet3D
Id: 6/8 Title: Duet 3 Mini 5+ - Wifi File: FETsBuffers.sch Sheet: /MOSFETs and Buffers/ Duet3D


3 RXD 4 VIO 5 CANL 6 CANH 7 S
L30 CM Choke C26

(c) Duet3D
Id: 7/8 Title: Duet 3 Mini 5+ - Wifi File: Comms.sch Sheet: /Comms/ Duet3D


Id: 8/8 Title: Duet 3 Mini 5+ - Wifi File: io.sch Sheet: /IO/ Duet3D

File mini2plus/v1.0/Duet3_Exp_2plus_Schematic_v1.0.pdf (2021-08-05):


Id: 1/1 Title: Duet 3 Exp 2+

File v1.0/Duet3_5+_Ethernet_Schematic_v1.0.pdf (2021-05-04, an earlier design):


Sheet: Headers File: Headers.sch Sheet: Power File: Power.sch

Sheet: Stepper Driver & Endstops

Id: 1/8 Title: Duet 3 Mini 5+ - Ethernet


www.duet3d.com
(c) Duet3D
Sheet: /Stepper Driver & Endstops/ Duet3D

File: Stepper_Drv.sch
Id: 2/8 Title: Duet 3 Mini 5+ - Ethernet


High Current Terminal HB9500-9.5 Power, MOSFET outputs

4 IO_0_OUT 5

Low/Medium Current Molex KK

(c) Duet3D
Id: 3/8 Title: Duet 3 Mini 5+ - Ethernet File: Headers.sch Sheet: /Headers/ Duet3D


5V Input, 3.3V Output for internal use only

5V Input, 3.3V Output for external use only

(c) Duet3D
Id: 4/8 Title: Duet 3 Mini 5+ - Ethernet File: Power.sch Sheet: /Power/ Duet3D


1 2 D5 ACT 180R R40 R100 1K (GND 5,31,38,45,53,64,78,90,96,106) (GNDANA 14,25) (VDDANA 6,15,26) (VDDIO 46,54,65,79,91,97,107,118) (VDDIOB 32,37) PA00 1 PA03 10

SWCLK also connected to act LED
SWDIO also connected to status LED

Review 1K pullup on SWCLK

Net-Tie

Id: 5/8 Title: Duet 3 Mini 5+ - Ethernet File: Processor.sch Sheet: /Processor/ Duet3D


OUT0 - OUT3 - High current MOSFETs FET Drives OUT 3 MOSFET CONTROL

(c) Duet3D
Id: 6/8 Title: Duet 3 Mini 5+ - Ethernet File: FETsBuffers.sch Sheet: /MOSFETs and Buffers/ Duet3D


1 MDIO 10 MDC 11 RXD1 12 RXD0 13 VDDIO 14 CRS_RV 15 REF_CLK 16 RXER 17

shield ground point uSD

the default is fine). CAN Transceiver

3 RXD 4 VIO 5 CANL 6 CANH 7 S

(c) Duet3D
Id: 7/8 Title: Duet 3 Mini 5+ - Ethernet File: Comms.sch Sheet: /Comms/ Duet3D


IO inputs (Used for endstops, probes, filament monitors and other low speed IO)

Id: 8/8 Title: Duet 3 Mini 5+ - Ethernet File: io.sch Sheet: /IO/ Duet3D

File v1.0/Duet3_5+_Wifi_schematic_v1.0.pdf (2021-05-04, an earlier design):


Sheet: Headers File: Headers.sch Sheet: Power File: Power.sch

Sheet: Stepper Driver & Endstops

Id: 1/8 Title: Duet 3 Mini 5+ - Wifi


(c) Duet3D
Sheet: /Stepper Driver & Endstops/ Duet3D

File: Stepper_Drv.sch
Id: 2/8 Title: Duet 3 Mini 5+ - Wifi


Test Points Motor Connectors

4 IO_0_OUT 5

Low/Medium Current Molex KK

(c) Duet3D
Id: 3/8 Title: Duet 3 Mini 5+ - Wifi File: Headers.sch Sheet: /Headers/ Duet3D


5V Input, 3.3V Output for internal use only

5V Input, 3.3V Output for external use only

(c) Duet3D
Id: 4/8 Title: Duet 3 Mini 5+ - Wifi File: Power.sch Sheet: /Power/ Duet3D


SWDIO also connected to status LED

F4 VSSA FUSE M7 MOUNTING M6 MOUNTING

Id: 5/8 Title: Duet 3 Mini 5+ - Wifi File: Processor.sch Sheet: /Processor/ Duet3D


OUT0 - OUT3 - High current MOSFETs FET Drives OUT 3 MOSFET CONTROL

(c) Duet3D
Id: 6/8 Title: Duet 3 Mini 5+ - Wifi File: FETsBuffers.sch Sheet: /MOSFETs and Buffers/ Duet3D


3 RXD 4 VIO 5 CANL 6 CANH 7 S
L30 CM Choke C26

(c) Duet3D
Id: 7/8 Title: Duet 3 Mini 5+ - Wifi File: Comms.sch Sheet: /Comms/ Duet3D


IO inputs (Used for endstops, probes, filament monitors and other low speed IO)

Id: 8/8 Title: Duet 3 Mini 5+ - Wifi File: io.sch Sheet: /IO/ Duet3D

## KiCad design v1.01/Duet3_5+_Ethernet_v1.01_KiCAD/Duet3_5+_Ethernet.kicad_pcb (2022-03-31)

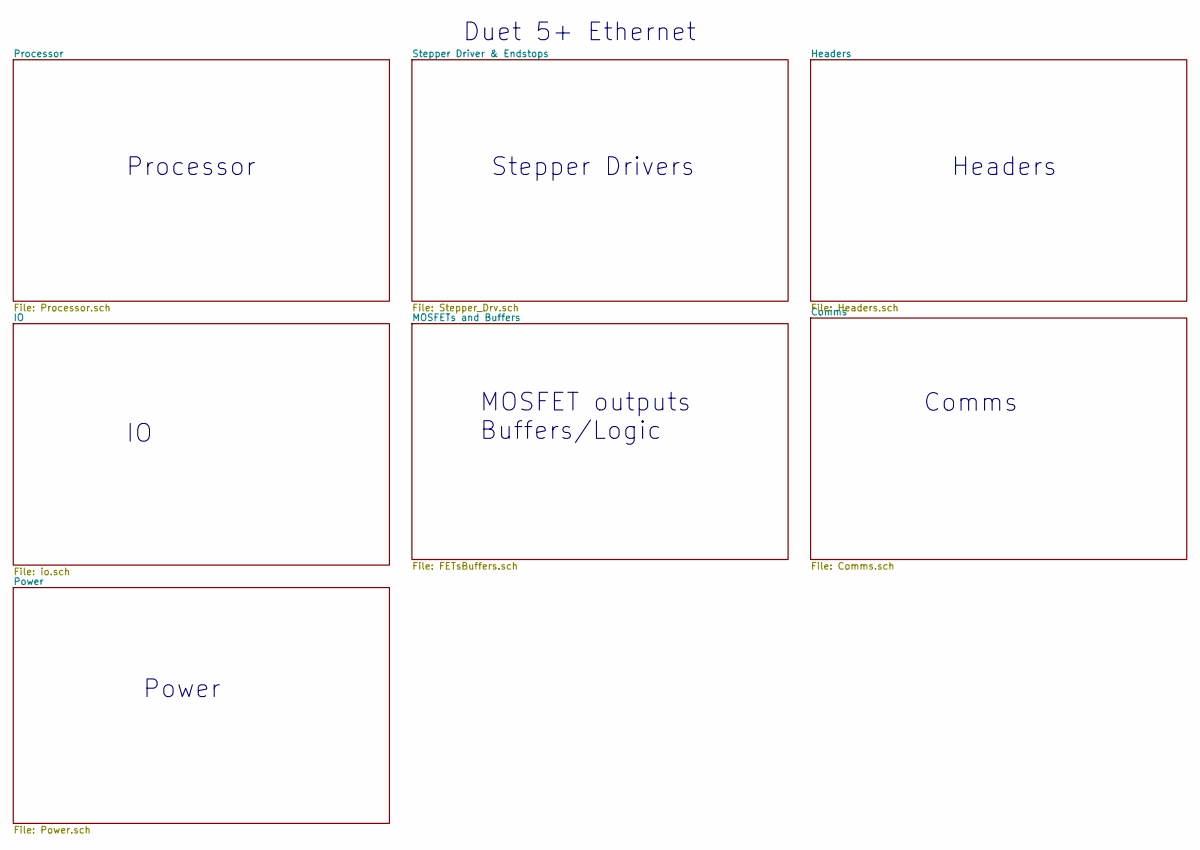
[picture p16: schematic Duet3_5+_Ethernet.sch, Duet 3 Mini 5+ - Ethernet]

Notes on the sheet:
Processor
Stepper Drivers
Headers
MOSFET outputs Buffers/Logic
Power
Duet 5+ Ethernet
Comms

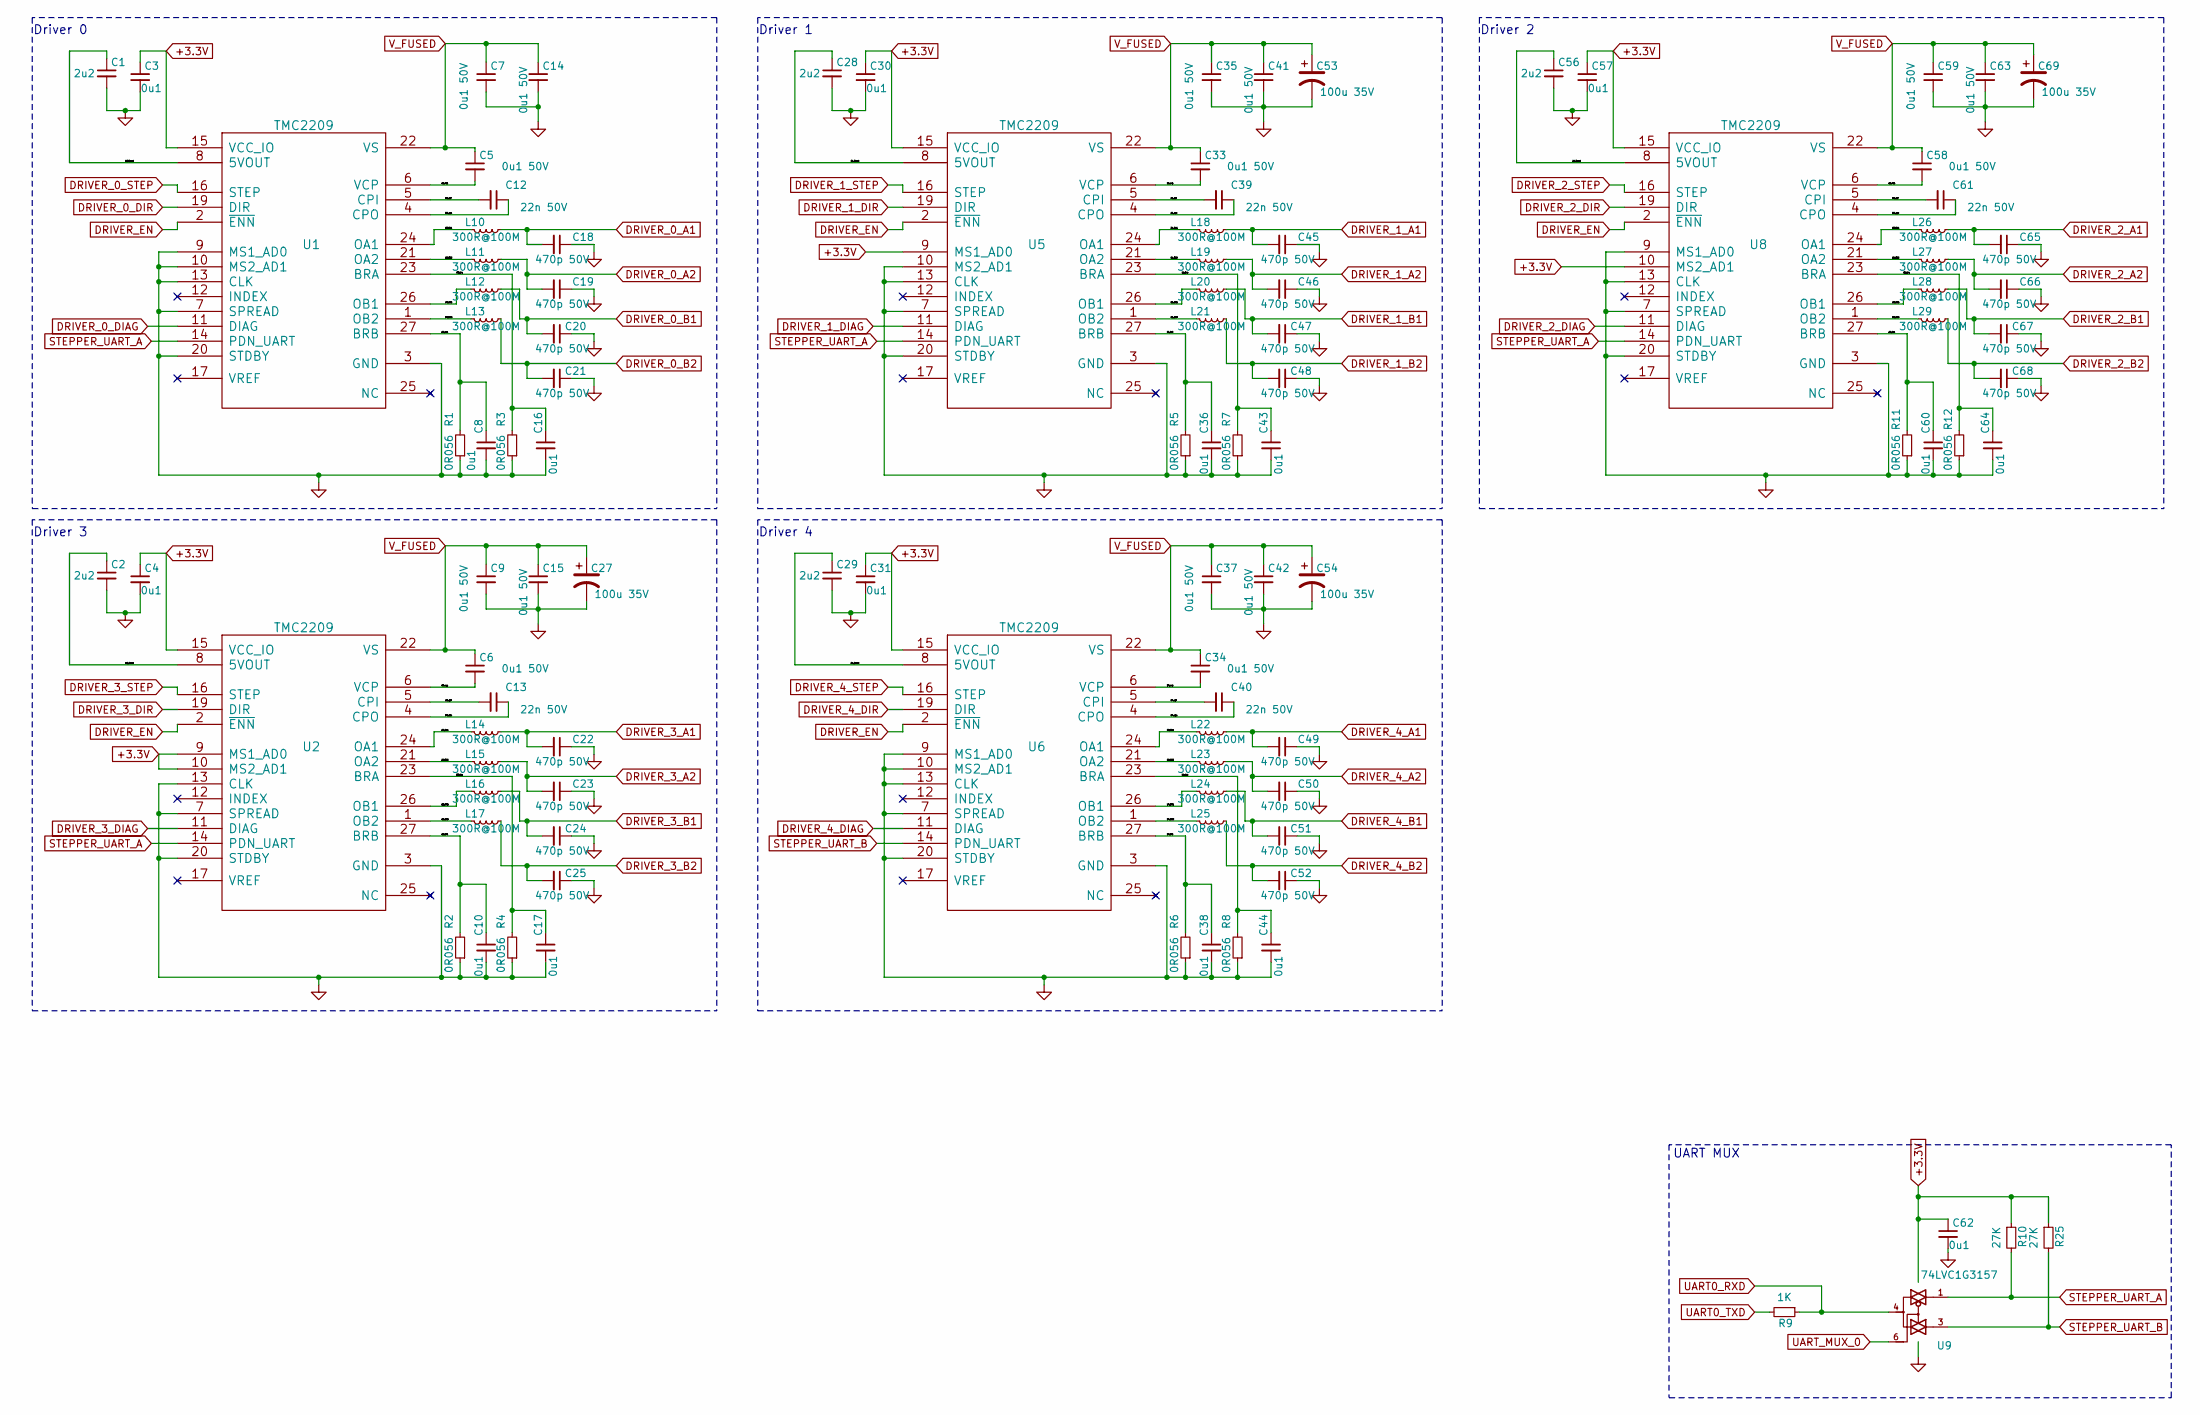
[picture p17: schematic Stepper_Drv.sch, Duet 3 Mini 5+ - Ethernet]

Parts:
C1, C2, C28, C29, C56: 2u2; C_0402_1005Metric_Wbry; Part Number LMK105BJ225KV-F or similar 10v+
C3, C4, C8, C10, C16, C17, C30, C31, C36, C38, C43, C44, C57, C60, C62, C64: 0u1; C_0402_1005Metric_Wbry; Part Number CL05A104KA5NNNC or similar
C5, C6, C7, C9, C14, C15, C33, C34, C35, C37, C41, C42, C58, C59, C63: 0u1 50V; C_0603_1608Metric_Wbry; Part Number CL10B104KB8NNNC
C12, C13, C39, C40, C61: 22n 50V; C_0402_1005Metric_Wbry; Part Number CC0402KRX7R9BB223
C18, C19, C20, C21, C22, C23, C24, C25, C45, C46, C47, C48, C49, C50, C51, C52, C65, C66, C67, C68: 470p 50V; C_0402_1005Metric_Wbry; Part Number CC0402KRX7R9BB471
C27, C53, C54, C69: 100u 35V; CP_Elec_6.3x7.7; Part Number e.g EEEFT1V101AP or 865080545012
L10, L11, L12, L13, L14, L15, L16, L17, L18, L19, L20, L21, L22, L23, L24, L25, L26, L27, L28, L29: 300R@100M; L_0603_1608Metric; Part Number 742792641 or similar
R1, R2, R3, R4, R5, R6, R7, R8, R11, R12: 0R056; R_0603_1608Metric_Wbry; Part Number 0603 0.33W or 0.5W 0.056R resistor
R9: 1K; R_0402_1005Metric_Wbry; Part Number RK73H1ETTP1001F
R10, R25: 27K; R_0402_1005Metric_Wbry; Part Number RK73H1ETTP2702F
U1, U2, U5, U6, U8: TMC2209; QFN-28-1EP_5x5mm_Pitch0.5mm; Part Number TMC2209-LA
U9: 74LVC1G3157; SOT-363_SC-70-6; Part Number 74LVC1G3157DW-7 (multiple options for 6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

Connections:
+3.3V: C3.1, C4.1, C30.1, C31.1, C57.1, C62.1, R10.1, R25.1, U1.15 (VCC_IO), U2.9 (MS1_AD0), U2.10 (MS2_AD1), U2.15 (VCC_IO), U5.9 (MS1_AD0), U5.15 (VCC_IO), U6.15 (VCC_IO), U8.10 (MS2_AD1), U8.15 (VCC_IO), U9.5 (VCC); also elsewhere on the board
/Stepper Driver & Endstops/D0_5vout: C1.1, U1.8 (5VOUT)
/Stepper Driver & Endstops/D0_OA1: L10.2, U1.24 (OA1)
/Stepper Driver & Endstops/D0_OA2: L11.2, U1.21 (OA2)
/Stepper Driver & Endstops/D0_OB1: L12.2, U1.26 (OB1)
/Stepper Driver & Endstops/D0_OB2: L13.2, U1.1 (OB2)
/Stepper Driver & Endstops/D0_bra: C16.1, R3.2, U1.23 (BRA)
/Stepper Driver & Endstops/D0_brb: C8.1, R1.2, U1.27 (BRB)
/Stepper Driver & Endstops/D0_cpi: C12.2, U1.5 (CPI)
/Stepper Driver & Endstops/D0_cpo: C12.1, U1.4 (CPO)
/Stepper Driver & Endstops/D0_vcp: C5.2, U1.6 (VCP)
/Stepper Driver & Endstops/D1_5vout: C28.1, U5.8 (5VOUT)
/Stepper Driver & Endstops/D1_OA1: L18.2, U5.24 (OA1)
/Stepper Driver & Endstops/D1_OA2: L19.2, U5.21 (OA2)
/Stepper Driver & Endstops/D1_OB1: L20.2, U5.26 (OB1)
/Stepper Driver & Endstops/D1_OB2: L21.2, U5.1 (OB2)
/Stepper Driver & Endstops/D1_bra: C43.1, R7.2, U5.23 (BRA)
/Stepper Driver & Endstops/D1_brb: C36.1, R5.2, U5.27 (BRB)
/Stepper Driver & Endstops/D1_cpi: C39.2, U5.5 (CPI)
/Stepper Driver & Endstops/D1_cpo: C39.1, U5.4 (CPO)
/Stepper Driver & Endstops/D1_vcp: C33.2, U5.6 (VCP)
/Stepper Driver & Endstops/D2_5vout: C56.1, U8.8 (5VOUT)
/Stepper Driver & Endstops/D2_OA1: L26.2, U8.24 (OA1)
/Stepper Driver & Endstops/D2_OA2: L27.2, U8.21 (OA2)
/Stepper Driver & Endstops/D2_OB1: L28.2, U8.26 (OB1)
/Stepper Driver & Endstops/D2_OB2: L29.2, U8.1 (OB2)
/Stepper Driver & Endstops/D2_bra: C64.1, R12.2, U8.23 (BRA)
/Stepper Driver & Endstops/D2_brb: C60.1, R11.2, U8.27 (BRB)
/Stepper Driver & Endstops/D2_cpi: C61.2, U8.5 (CPI)
/Stepper Driver & Endstops/D2_cpo: C61.1, U8.4 (CPO)
/Stepper Driver & Endstops/D2_vcp: C58.2, U8.6 (VCP)
/Stepper Driver & Endstops/D3_5vout: C2.1, U2.8 (5VOUT)
/Stepper Driver & Endstops/D3_OA1: L14.2, U2.24 (OA1)
/Stepper Driver & Endstops/D3_OA2: L15.2, U2.21 (OA2)
/Stepper Driver & Endstops/D3_OB1: L16.2, U2.26 (OB1)
/Stepper Driver & Endstops/D3_OB2: L17.2, U2.1 (OB2)
/Stepper Driver & Endstops/D3_bra: C17.1, R4.2, U2.23 (BRA)
/Stepper Driver & Endstops/D3_brb: C10.1, R2.2, U2.27 (BRB)
/Stepper Driver & Endstops/D3_cpi: C13.2, U2.5 (CPI)
/Stepper Driver & Endstops/D3_cpo: C13.1, U2.4 (CPO)
/Stepper Driver & Endstops/D3_vcp: C6.2, U2.6 (VCP)
/Stepper Driver & Endstops/D4_5vout: C29.1, U6.8 (5VOUT)
/Stepper Driver & Endstops/D4_OA1: L22.2, U6.24 (OA1)
/Stepper Driver & Endstops/D4_OA2: L23.2, U6.21 (OA2)
/Stepper Driver & Endstops/D4_OB1: L24.2, U6.26 (OB1)
/Stepper Driver & Endstops/D4_OB2: L25.2, U6.1 (OB2)
/Stepper Driver & Endstops/D4_bra: C44.1, R8.2, U6.23 (BRA)
/Stepper Driver & Endstops/D4_brb: C38.1, R6.2, U6.27 (BRB)
/Stepper Driver & Endstops/D4_cpi: C40.2, U6.5 (CPI)
/Stepper Driver & Endstops/D4_cpo: C40.1, U6.4 (CPO)
/Stepper Driver & Endstops/D4_vcp: C34.2, U6.6 (VCP)
DRIVER_0_A1: C18.2, L10.1; also elsewhere on the board
DRIVER_0_A2: C19.2, L11.1; also elsewhere on the board
DRIVER_0_B1: C20.2, L12.1; also elsewhere on the board
DRIVER_0_B2: C21.2, L13.1; also elsewhere on the board
DRIVER_0_DIAG: U1.11 (DIAG); also elsewhere on the board
DRIVER_0_DIR: U1.19 (DIR); also elsewhere on the board
DRIVER_0_STEP: U1.16 (STEP); also elsewhere on the board
DRIVER_1_A1: C45.2, L18.1; also elsewhere on the board
DRIVER_1_A2: C46.2, L19.1; also elsewhere on the board
DRIVER_1_B1: C47.2, L20.1; also elsewhere on the board
DRIVER_1_B2: C48.2, L21.1; also elsewhere on the board
DRIVER_1_DIAG: U5.11 (DIAG); also elsewhere on the board
DRIVER_1_DIR: U5.19 (DIR); also elsewhere on the board
DRIVER_1_STEP: U5.16 (STEP); also elsewhere on the board
DRIVER_2_A1: C65.2, L26.1; also elsewhere on the board
DRIVER_2_A2: C66.2, L27.1; also elsewhere on the board
DRIVER_2_B1: C67.2, L28.1; also elsewhere on the board
DRIVER_2_B2: C68.2, L29.1; also elsewhere on the board
DRIVER_2_DIAG: U8.11 (DIAG); also elsewhere on the board
DRIVER_2_DIR: U8.19 (DIR); also elsewhere on the board
DRIVER_2_STEP: U8.16 (STEP); also elsewhere on the board
DRIVER_3_A1: C22.2, L14.1; also elsewhere on the board
DRIVER_3_A2: C23.2, L15.1; also elsewhere on the board
DRIVER_3_B1: C24.2, L16.1; also elsewhere on the board
DRIVER_3_B2: C25.2, L17.1; also elsewhere on the board
DRIVER_3_DIAG: U2.11 (DIAG); also elsewhere on the board
DRIVER_3_DIR: U2.19 (DIR); also elsewhere on the board
DRIVER_3_STEP: U2.16 (STEP); also elsewhere on the board
DRIVER_4_A1: C49.2, L22.1; also elsewhere on the board
DRIVER_4_A2: C50.2, L23.1; also elsewhere on the board
DRIVER_4_B1: C51.2, L24.1; also elsewhere on the board
DRIVER_4_B2: C52.2, L25.1; also elsewhere on the board
DRIVER_4_DIAG: U6.11 (DIAG); also elsewhere on the board
DRIVER_4_DIR: U6.19 (DIR); also elsewhere on the board
DRIVER_4_STEP: U6.16 (STEP); also elsewhere on the board
DRIVER_EN: U1.2 (~ENN), U2.2 (~ENN), U5.2 (~ENN), U6.2 (~ENN), U8.2 (~ENN); also elsewhere on the board
GND: C1.2, C2.2, C3.2, C4.2, C7.2, C8.2, C9.2, C10.2, C14.2, C15.2, C16.2, C17.2, C18.1, C19.1, C20.1, C21.1, C22.1, C23.1, C24.1, C25.1, C27.2, C28.2, C29.2, C30.2, C31.2, C35.2, C36.2, C37.2, C38.2, C41.2, C42.2, C43.2, C44.2, C45.1, C46.1, C47.1, C48.1, C49.1, C50.1, C51.1, C52.1, C53.2, C54.2, C56.2, C57.2, C59.2, C60.2, C62.2, C63.2, C64.2, C65.1, C66.1, C67.1, C68.1, C69.2, R1.1, R2.1, R3.1, R4.1, R5.1, R6.1, R7.1, R8.1, R11.1, R12.1, U1.3 (GND), U1.7 (SPREAD), U1.9 (MS1_AD0), U1.10 (MS2_AD1), U1.13 (CLK), U1.18 (GND), U1.20 (STDBY), U1.29 (GND), U2.3 (GND), U2.7 (SPREAD), U2.13 (CLK), U2.18 (GND), U2.20 (STDBY), U2.29 (GND), U5.3 (GND), U5.7 (SPREAD), U5.10 (MS2_AD1), U5.13 (CLK), U5.18 (GND), U5.20 (STDBY), U5.29 (GND), U6.3 (GND), U6.7 (SPREAD), U6.9 (MS1_AD0), U6.10 (MS2_AD1), U6.13 (CLK), U6.18 (GND), U6.20 (STDBY), U6.29 (GND), U8.3 (GND), U8.7 (SPREAD), U8.9 (MS1_AD0), U8.13 (CLK), U8.18 (GND), U8.20 (STDBY), U8.29 (GND), U9.2 (GND); also elsewhere on the board
STEPPER_UART_A: R10.2, U1.14 (PDN_UART), U2.14 (PDN_UART), U5.14 (PDN_UART), U8.14 (PDN_UART), U9.1
STEPPER_UART_B: R25.2, U6.14 (PDN_UART), U9.3; also elsewhere on the board
UART0_RXD: R9.1, U9.4; also elsewhere on the board
UART0_TXD: R9.2; also elsewhere on the board
UART_MUX_0: U9.6; also elsewhere on the board
V_FUSED: C5.1, C6.1, C7.1, C9.1, C14.1, C15.1, C27.1, C33.1, C34.1, C35.1, C37.1, C41.1, C42.1, C53.1, C54.1, C58.1, C59.1, C63.1, C69.1, U1.22 (VS), U1.28 (VS), U2.22 (VS), U2.28 (VS), U5.22 (VS), U5.28 (VS), U6.22 (VS), U6.28 (VS), U8.22 (VS), U8.28 (VS); also elsewhere on the board

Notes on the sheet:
Driver 0
UART MUX
Driver 1
Driver 2
Driver 3
Driver 4

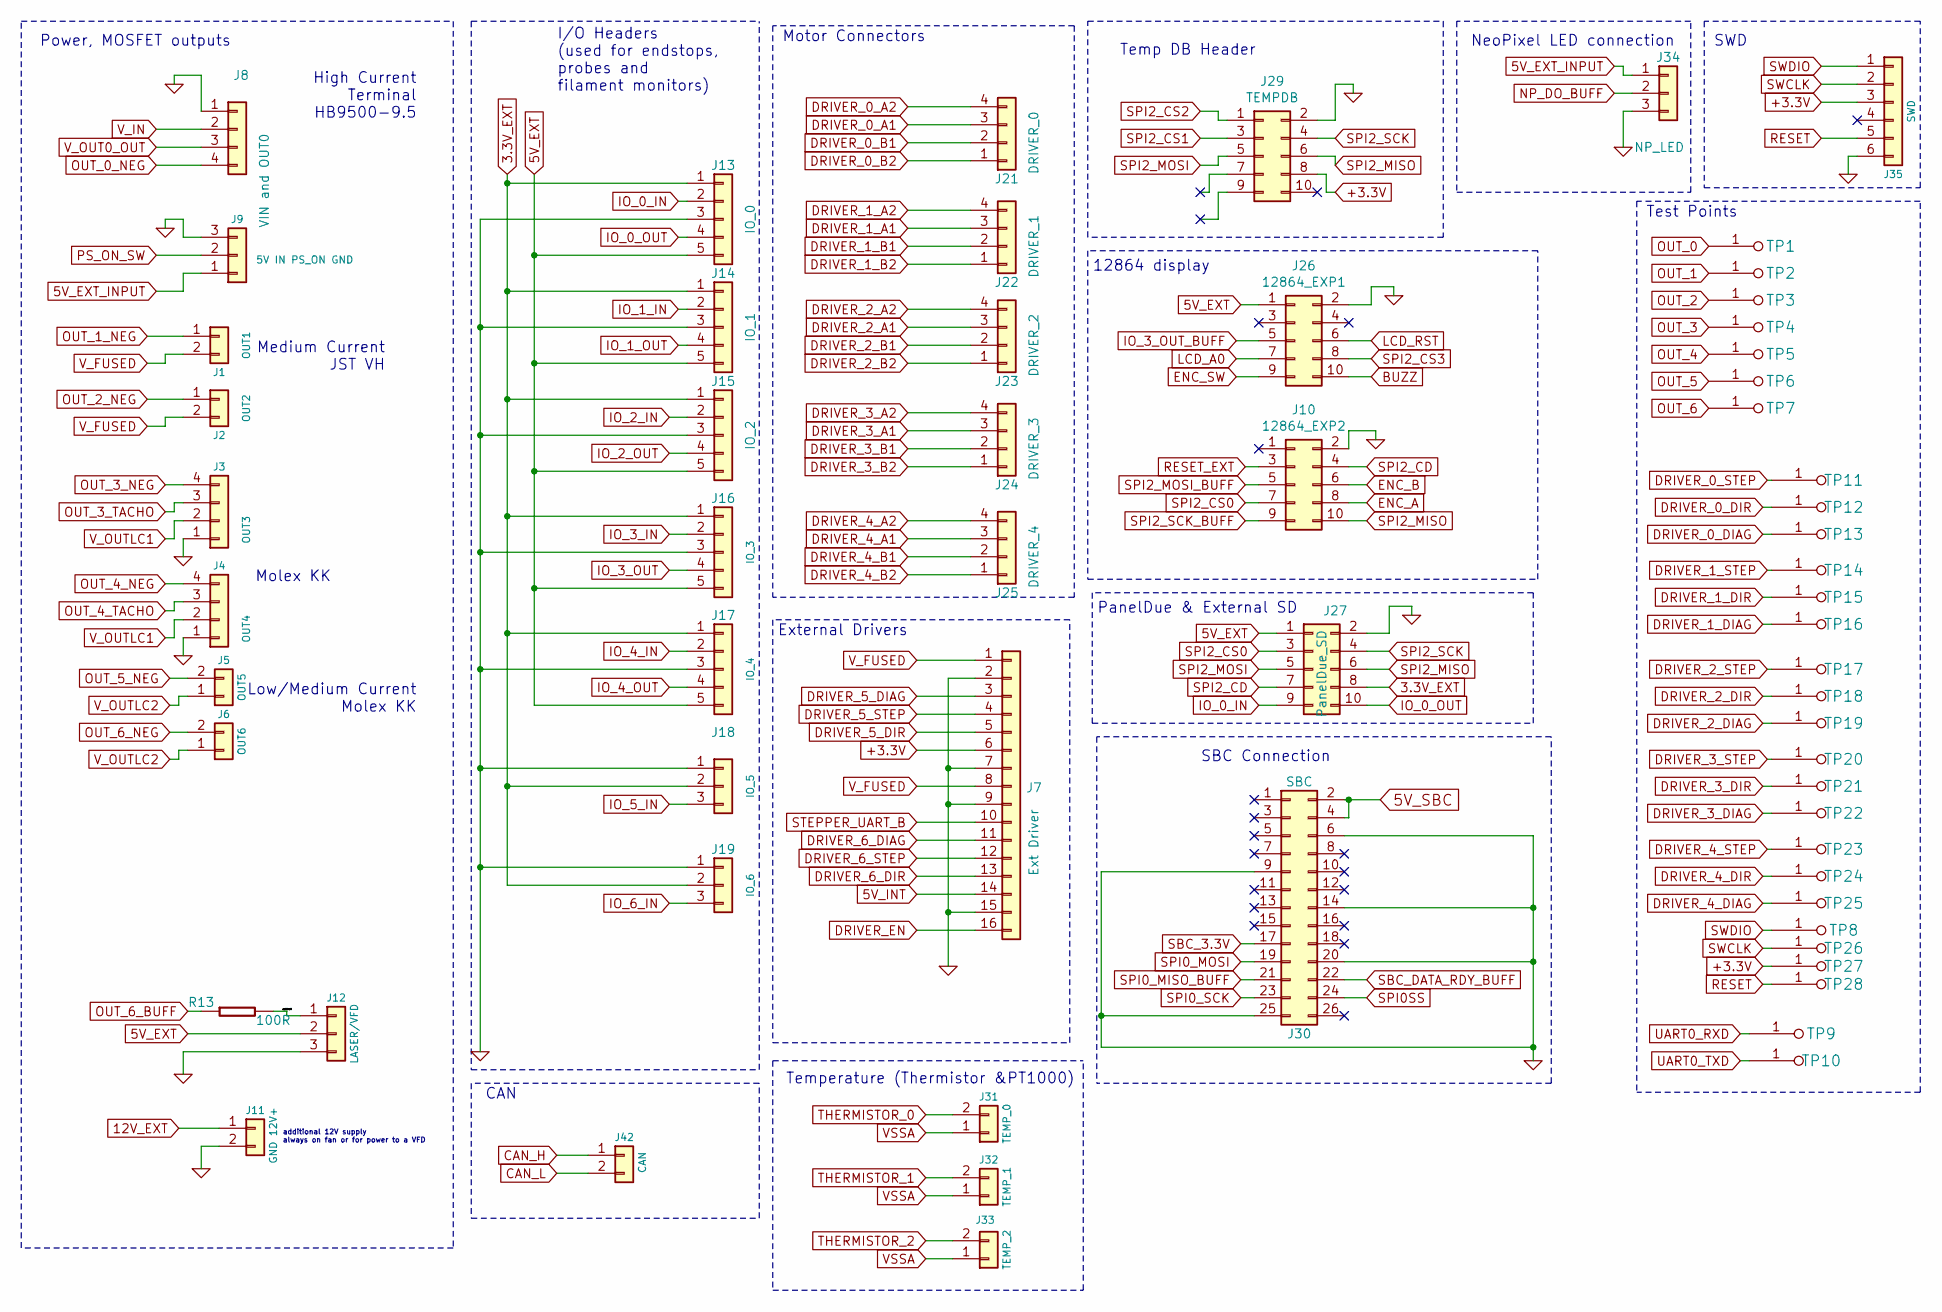
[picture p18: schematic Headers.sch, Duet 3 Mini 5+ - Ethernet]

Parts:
J1: OUT1; JST_VH_B2P-VH-B_1x02_P3.96mm_Vertical; Part Number B2P-VH(LF)(SN)
J2: OUT2; JST_VH_B2P-VH-B_1x02_P3.96mm_Vertical; Part Number B2P-VH(LF)(SN)
J3: OUT3; Wurth_61900411121-1x04_P2.54mm_Vertical(Molex_KK-254_AE-641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; Part Number 61900411121
J4: OUT4; Wurth_61900411121-1x04_P2.54mm_Vertical(Molex_KK-254_AE-641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; Part Number 61900411121
J5: OUT5; Wurth_61900211121-1x02_P2.54mm_Vertical-(Molex_KK-254_AE-64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; Part Number 61900211121
J6: OUT6; Wurth_61900211121-1x02_P2.54mm_Vertical-(Molex_KK-254_AE-64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; Part Number 61900211121
J7: Ext Driver; D3_mini2Plus_expansion_1x16; Part Number THS-20-R
J8: VIN and OUT0; screwt-barrier-9.5mm-1x4; Part Number HB950-9.50-4P
J9: 5V IN PS_ON GND; Wurth_61900311121-1x03_P2.54mm_Vertical(Molex_KK-254_AE-641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; Part Number 61900311121
J10: 12864_EXP2; IDC-Header_2x05_P2.54mm_Vertical; Part Number 302-S-10-D1R1
J11: GND 12V+; Wurth_61900211121-1x02_P2.54mm_Vertical-(Molex_KK-254_AE-64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; Part Number 61900211121
J12: LASER/VFD; Wurth_61900311121-1x03_P2.54mm_Vertical(Molex_KK-254_AE-641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; Part Number 61900311121
J13: IO_0; Wurth_61900511121-1x05_P2.54mm_Vertical(Molex_KK-254_AE-641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; Part Number 61900511121
J14: IO_1; Wurth_61900511121-1x05_P2.54mm_Vertical(Molex_KK-254_AE-641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; Part Number 61900511121
J15: IO_2; Wurth_61900511121-1x05_P2.54mm_Vertical(Molex_KK-254_AE-641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; Part Number 61900511121
J16: IO_3; Wurth_61900511121-1x05_P2.54mm_Vertical(Molex_KK-254_AE-641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; Part Number 61900511121
J17: IO_4; Wurth_61900511121-1x05_P2.54mm_Vertical(Molex_KK-254_AE-641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; Part Number 61900511121
J18: IO_5; Wurth_61900311121-1x03_P2.54mm_Vertical(Molex_KK-254_AE-641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; Part Number 61900311121
J19: IO_6; Wurth_61900311121-1x03_P2.54mm_Vertical(Molex_KK-254_AE-641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; Part Number 61900311121
J21: DRIVER_0; Wurth_61900411121-1x04_P2.54mm_Vertical(Molex_KK-254_AE-641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; Part Number 61900411121
J22: DRIVER_1; Wurth_61900411121-1x04_P2.54mm_Vertical(Molex_KK-254_AE-641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; Part Number 61900411121
J23: DRIVER_2; Wurth_61900411121-1x04_P2.54mm_Vertical(Molex_KK-254_AE-641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; Part Number 61900411121
J24: DRIVER_3; Wurth_61900411121-1x04_P2.54mm_Vertical(Molex_KK-254_AE-641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; Part Number 61900411121
J25: DRIVER_4; Wurth_61900411121-1x04_P2.54mm_Vertical(Molex_KK-254_AE-641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; Part Number 61900411121
J26: 12864_EXP1; IDC-Header_2x05_P2.54mm_Vertical; Part Number 302-S-10-D1R1
J27: PanelDue_SD; IDC-Header_2x05_P2.54mm_Vertical; Part Number 302-S-10-D1R1
J29: TEMPDB; MAX_TEMP_DB; Part Number THD-05-R
J30: SBC; IDC-Header_2x13_P2.54mm_Vertical; Part Number 61202621621
J31: TEMP_0; Wurth_61900211121-1x02_P2.54mm_Vertical-(Molex_KK-254_AE-64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; Part Number 61900211121
J32: TEMP_1; Wurth_61900211121-1x02_P2.54mm_Vertical-(Molex_KK-254_AE-64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; Part Number 61900211121
J33: TEMP_2; Wurth_61900211121-1x02_P2.54mm_Vertical-(Molex_KK-254_AE-64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; Part Number 61900211121
J34: NP_LED; Wurth_61900311121-1x03_P2.54mm_Vertical(Molex_KK-254_AE-641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; Part Number 61900311121
J35: SWD; JST_ZH_1x06_P1.5_B6B-ZR-SM4-TF; Part Number DNP - B6B-ZR(LF)(SN)
J42: CAN; Wurth_61900211121-1x02_P2.54mm_Vertical-(Molex_KK-254_AE-64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; Part Number 61900211121
R13: 100R; R_0402_1005Metric_Wbry; Part Number RK73H1ETTP1000F
TP1: OUT_0; TestPoint_Pad_D1.0mm; Part Number DNP - Virtual component
TP2: OUT_1; TestPoint_Pad_D1.0mm; Part Number DNP - Virtual component
TP3: OUT_2; TestPoint_Pad_D1.0mm; Part Number DNP - Virtual component
TP4: OUT_3; TestPoint_Pad_D1.0mm; Part Number DNP - Virtual component
TP5: OUT_4; TestPoint_Pad_D1.0mm; Part Number DNP - Virtual component
TP6: OUT_5; TestPoint_Pad_D1.0mm; Part Number DNP - Virtual component
TP7: OUT_6; TestPoint_Pad_D1.0mm; Part Number DNP - Virtual component
TP8: SWDIO; TestPoint_Pad_D1.5mm; Part Number DNP - Virtual component
TP9: UART0_RXD; TestPoint_Pad_D1.0mm; Part Number DNP - Virtual component
TP10: UART0_TXD; TestPoint_Pad_D1.0mm; Part Number DNP - Virtual component
TP11: D0_STEP; TestPoint_Pad_D1.0mm; Part Number DNP - Virtual component
TP12: D0_DIR; TestPoint_Pad_D1.0mm; Part Number DNP - Virtual component
TP13: D0_DIAG0; TestPoint_Pad_D1.0mm; Part Number DNP - Virtual component
TP14: D1_STEP; TestPoint_Pad_D1.0mm; Part Number DNP - Virtual component
TP15: D1_DIR; TestPoint_Pad_D1.0mm; Part Number DNP - Virtual component
TP16: D1_DIAG0; TestPoint_Pad_D1.0mm; Part Number DNP - Virtual component
TP17: D2_STEP; TestPoint_Pad_D1.0mm; Part Number DNP - Virtual component
TP18: D2_DIR; TestPoint_Pad_D1.0mm; Part Number DNP - Virtual component
TP19: D2_DIAG0; TestPoint_Pad_D1.0mm; Part Number DNP - Virtual component
TP20: D3_STEP; TestPoint_Pad_D1.0mm; Part Number DNP - Virtual component
TP21: D3_DIR; TestPoint_Pad_D1.0mm; Part Number DNP - Virtual component
TP22: D3_DIAG0; TestPoint_Pad_D1.0mm; Part Number DNP - Virtual component
TP23: D4_STEP; TestPoint_Pad_D1.0mm; Part Number DNP - Virtual component
TP24: D4_DIR; TestPoint_Pad_D1.0mm; Part Number DNP - Virtual component
TP25: D4_DIAG0; TestPoint_Pad_D1.0mm; Part Number DNP - Virtual component
TP26: SWCLK; TestPoint_Pad_D1.5mm; Part Number DNP - Virtual component
TP27: +3.3V; TestPoint_Pad_D1.5mm; Part Number DNP - Virtual component
TP28: RESET; TestPoint_Pad_D1.5mm; Part Number DNP - Virtual component

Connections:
3.3V_EXT: J13.1, J14.1, J15.1, J16.1, J17.1, J18.2, J19.2, J27.8; also elsewhere on the board
5V_EXT: J12.2, J13.5, J14.5, J15.5, J16.5, J17.5, J26.1, J27.1; also elsewhere on the board
5V_EXT_INPUT: J9.1, J34.1; also elsewhere on the board
5V_INT: J7.14; also elsewhere on the board
5V_SBC: J30.2, J30.4; also elsewhere on the board
12V_EXT: J11.1; also elsewhere on the board
+3.3V: J7.6, J29.8, J35.3, TP27.1; also elsewhere on the board
/Headers/out6buff: J12.1, R13.2
BUZZ: J26.10; also elsewhere on the board
CAN_H: J42.1; also elsewhere on the board
CAN_L: J42.2; also elsewhere on the board
DRIVER_0_A1: J21.3; also elsewhere on the board
DRIVER_0_A2: J21.4; also elsewhere on the board
DRIVER_0_B1: J21.2; also elsewhere on the board
DRIVER_0_B2: J21.1; also elsewhere on the board
DRIVER_0_DIAG: TP13.1; also elsewhere on the board
DRIVER_0_DIR: TP12.1; also elsewhere on the board
DRIVER_0_STEP: TP11.1; also elsewhere on the board
DRIVER_1_A1: J22.3; also elsewhere on the board
DRIVER_1_A2: J22.4; also elsewhere on the board
DRIVER_1_B1: J22.2; also elsewhere on the board
DRIVER_1_B2: J22.1; also elsewhere on the board
DRIVER_1_DIAG: TP16.1; also elsewhere on the board
DRIVER_1_DIR: TP15.1; also elsewhere on the board
DRIVER_1_STEP: TP14.1; also elsewhere on the board
DRIVER_2_A1: J23.3; also elsewhere on the board
DRIVER_2_A2: J23.4; also elsewhere on the board
DRIVER_2_B1: J23.2; also elsewhere on the board
DRIVER_2_B2: J23.1; also elsewhere on the board
DRIVER_2_DIAG: TP19.1; also elsewhere on the board
DRIVER_2_DIR: TP18.1; also elsewhere on the board
DRIVER_2_STEP: TP17.1; also elsewhere on the board
DRIVER_3_A1: J24.3; also elsewhere on the board
DRIVER_3_A2: J24.4; also elsewhere on the board
DRIVER_3_B1: J24.2; also elsewhere on the board
DRIVER_3_B2: J24.1; also elsewhere on the board
DRIVER_3_DIAG: TP22.1; also elsewhere on the board
DRIVER_3_DIR: TP21.1; also elsewhere on the board
DRIVER_3_STEP: TP20.1; also elsewhere on the board
DRIVER_4_A1: J25.3; also elsewhere on the board
DRIVER_4_A2: J25.4; also elsewhere on the board
DRIVER_4_B1: J25.2; also elsewhere on the board
DRIVER_4_B2: J25.1; also elsewhere on the board
DRIVER_4_DIAG: TP25.1; also elsewhere on the board
DRIVER_4_DIR: TP24.1; also elsewhere on the board
DRIVER_4_STEP: TP23.1; also elsewhere on the board
DRIVER_5_DIAG: J7.3; also elsewhere on the board
DRIVER_5_DIR: J7.5; also elsewhere on the board
DRIVER_5_STEP: J7.4; also elsewhere on the board
DRIVER_6_DIAG: J7.11; also elsewhere on the board
DRIVER_6_DIR: J7.13; also elsewhere on the board
DRIVER_6_STEP: J7.12; also elsewhere on the board
DRIVER_EN: J7.16; also elsewhere on the board
ENC_A: J10.8; also elsewhere on the board
ENC_B: J10.6; also elsewhere on the board
ENC_SW: J26.9; also elsewhere on the board
GND: J3.1, J4.1, J7.2, J7.7, J7.9, J7.15, J8.1, J9.3, J10.2, J11.2, J12.3, J13.3, J14.3, J15.3, J16.3, J17.3, J18.1, J19.1, J26.2, J27.2, J29.2, J30.6, J30.9, J30.14, J30.20, J30.25, J34.3, J35.6; also elsewhere on the board
IO_0_IN: J13.2, J27.9; also elsewhere on the board
IO_0_OUT: J13.4, J27.10; also elsewhere on the board
IO_1_IN: J14.2; also elsewhere on the board
IO_1_OUT: J14.4; also elsewhere on the board
IO_2_IN: J15.2; also elsewhere on the board
IO_2_OUT: J15.4; also elsewhere on the board
IO_3_IN: J16.2; also elsewhere on the board
IO_3_OUT: J16.4; also elsewhere on the board
IO_3_OUT_BUFF: J26.5; also elsewhere on the board
IO_4_IN: J17.2; also elsewhere on the board
IO_4_OUT: J17.4; also elsewhere on the board
IO_5_IN: J18.3; also elsewhere on the board
IO_6_IN: J19.3; also elsewhere on the board
LCD_A0: J26.7; also elsewhere on the board
LCD_RST: J26.6; also elsewhere on the board
NP_DO_BUFF: J34.2; also elsewhere on the board
OUT_0: TP1.1; also elsewhere on the board
OUT_0_NEG: J8.4; also elsewhere on the board
OUT_1: TP2.1; also elsewhere on the board
OUT_1_NEG: J1.1; also elsewhere on the board
OUT_2: TP3.1; also elsewhere on the board
OUT_2_NEG: J2.1; also elsewhere on the board
OUT_3: TP4.1; also elsewhere on the board
OUT_3_NEG: J3.4; also elsewhere on the board
OUT_3_TACHO: J3.3; also elsewhere on the board
OUT_4: TP5.1; also elsewhere on the board
OUT_4_NEG: J4.4; also elsewhere on the board
OUT_4_TACHO: J4.3; also elsewhere on the board
OUT_5: TP6.1; also elsewhere on the board
OUT_5_NEG: J5.2; also elsewhere on the board
OUT_6: TP7.1; also elsewhere on the board
OUT_6_BUFF: R13.1; also elsewhere on the board
OUT_6_NEG: J6.2; also elsewhere on the board
PS_ON_SW: J9.2; also elsewhere on the board
RESET: J35.5, TP28.1; also elsewhere on the board
RESET_EXT: J10.3; also elsewhere on the board
SBC_3.3V: J30.17; also elsewhere on the board
SBC_DATA_RDY_BUFF: J30.22; also elsewhere on the board
SPI0SS: J30.24; also elsewhere on the board
SPI0_MISO_BUFF: J30.21; also elsewhere on the board
SPI0_MOSI: J30.19; also elsewhere on the board
SPI0_SCK: J30.23; also elsewhere on the board
SPI2_CD: J10.4, J27.7; also elsewhere on the board
SPI2_CS0: J10.7, J27.3; also elsewhere on the board
SPI2_CS1: J29.3; also elsewhere on the board
SPI2_CS2: J29.1; also elsewhere on the board
SPI2_CS3: J26.8; also elsewhere on the board
SPI2_MISO: J10.10, J27.6, J29.6; also elsewhere on the board
SPI2_MOSI: J27.5, J29.5; also elsewhere on the board
SPI2_MOSI_BUFF: J10.5; also elsewhere on the board
SPI2_SCK: J27.4, J29.4; also elsewhere on the board
SPI2_SCK_BUFF: J10.9; also elsewhere on the board
STEPPER_UART_B: J7.10; also elsewhere on the board
SWCLK: J35.2, TP26.1; also elsewhere on the board
SWDIO: J35.1, TP8.1; also elsewhere on the board
THERMISTOR_0: J31.2; also elsewhere on the board
THERMISTOR_1: J32.2; also elsewhere on the board
THERMISTOR_2: J33.2; also elsewhere on the board
UART0_RXD: TP9.1; also elsewhere on the board
UART0_TXD: TP10.1; also elsewhere on the board
VSSA: J31.1, J32.1, J33.1; also elsewhere on the board
V_FUSED: J1.2, J2.2, J7.1, J7.8; also elsewhere on the board
V_IN: J8.2; also elsewhere on the board
V_OUT0_OUT: J8.3; also elsewhere on the board
V_OUTLC1: J3.2, J4.2; also elsewhere on the board
V_OUTLC2: J5.1, J6.1; also elsewhere on the board

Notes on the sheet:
High Current Terminal HB9500-9.5
Power, MOSFET outputs
Temperature (Thermistor &PT1000)
Motor Connectors
Test Points
Medium Current JST VH
Temp DB Header
Low/Medium Current Molex KK
I/O Headers (used for endstops, probes and filament monitors)
Molex KK
NeoPixel LED connection
SWD
SBC Connection
additional 12V supply always on fan or for power to a VFD
External Drivers
PanelDue & External SD
12864 display
CAN

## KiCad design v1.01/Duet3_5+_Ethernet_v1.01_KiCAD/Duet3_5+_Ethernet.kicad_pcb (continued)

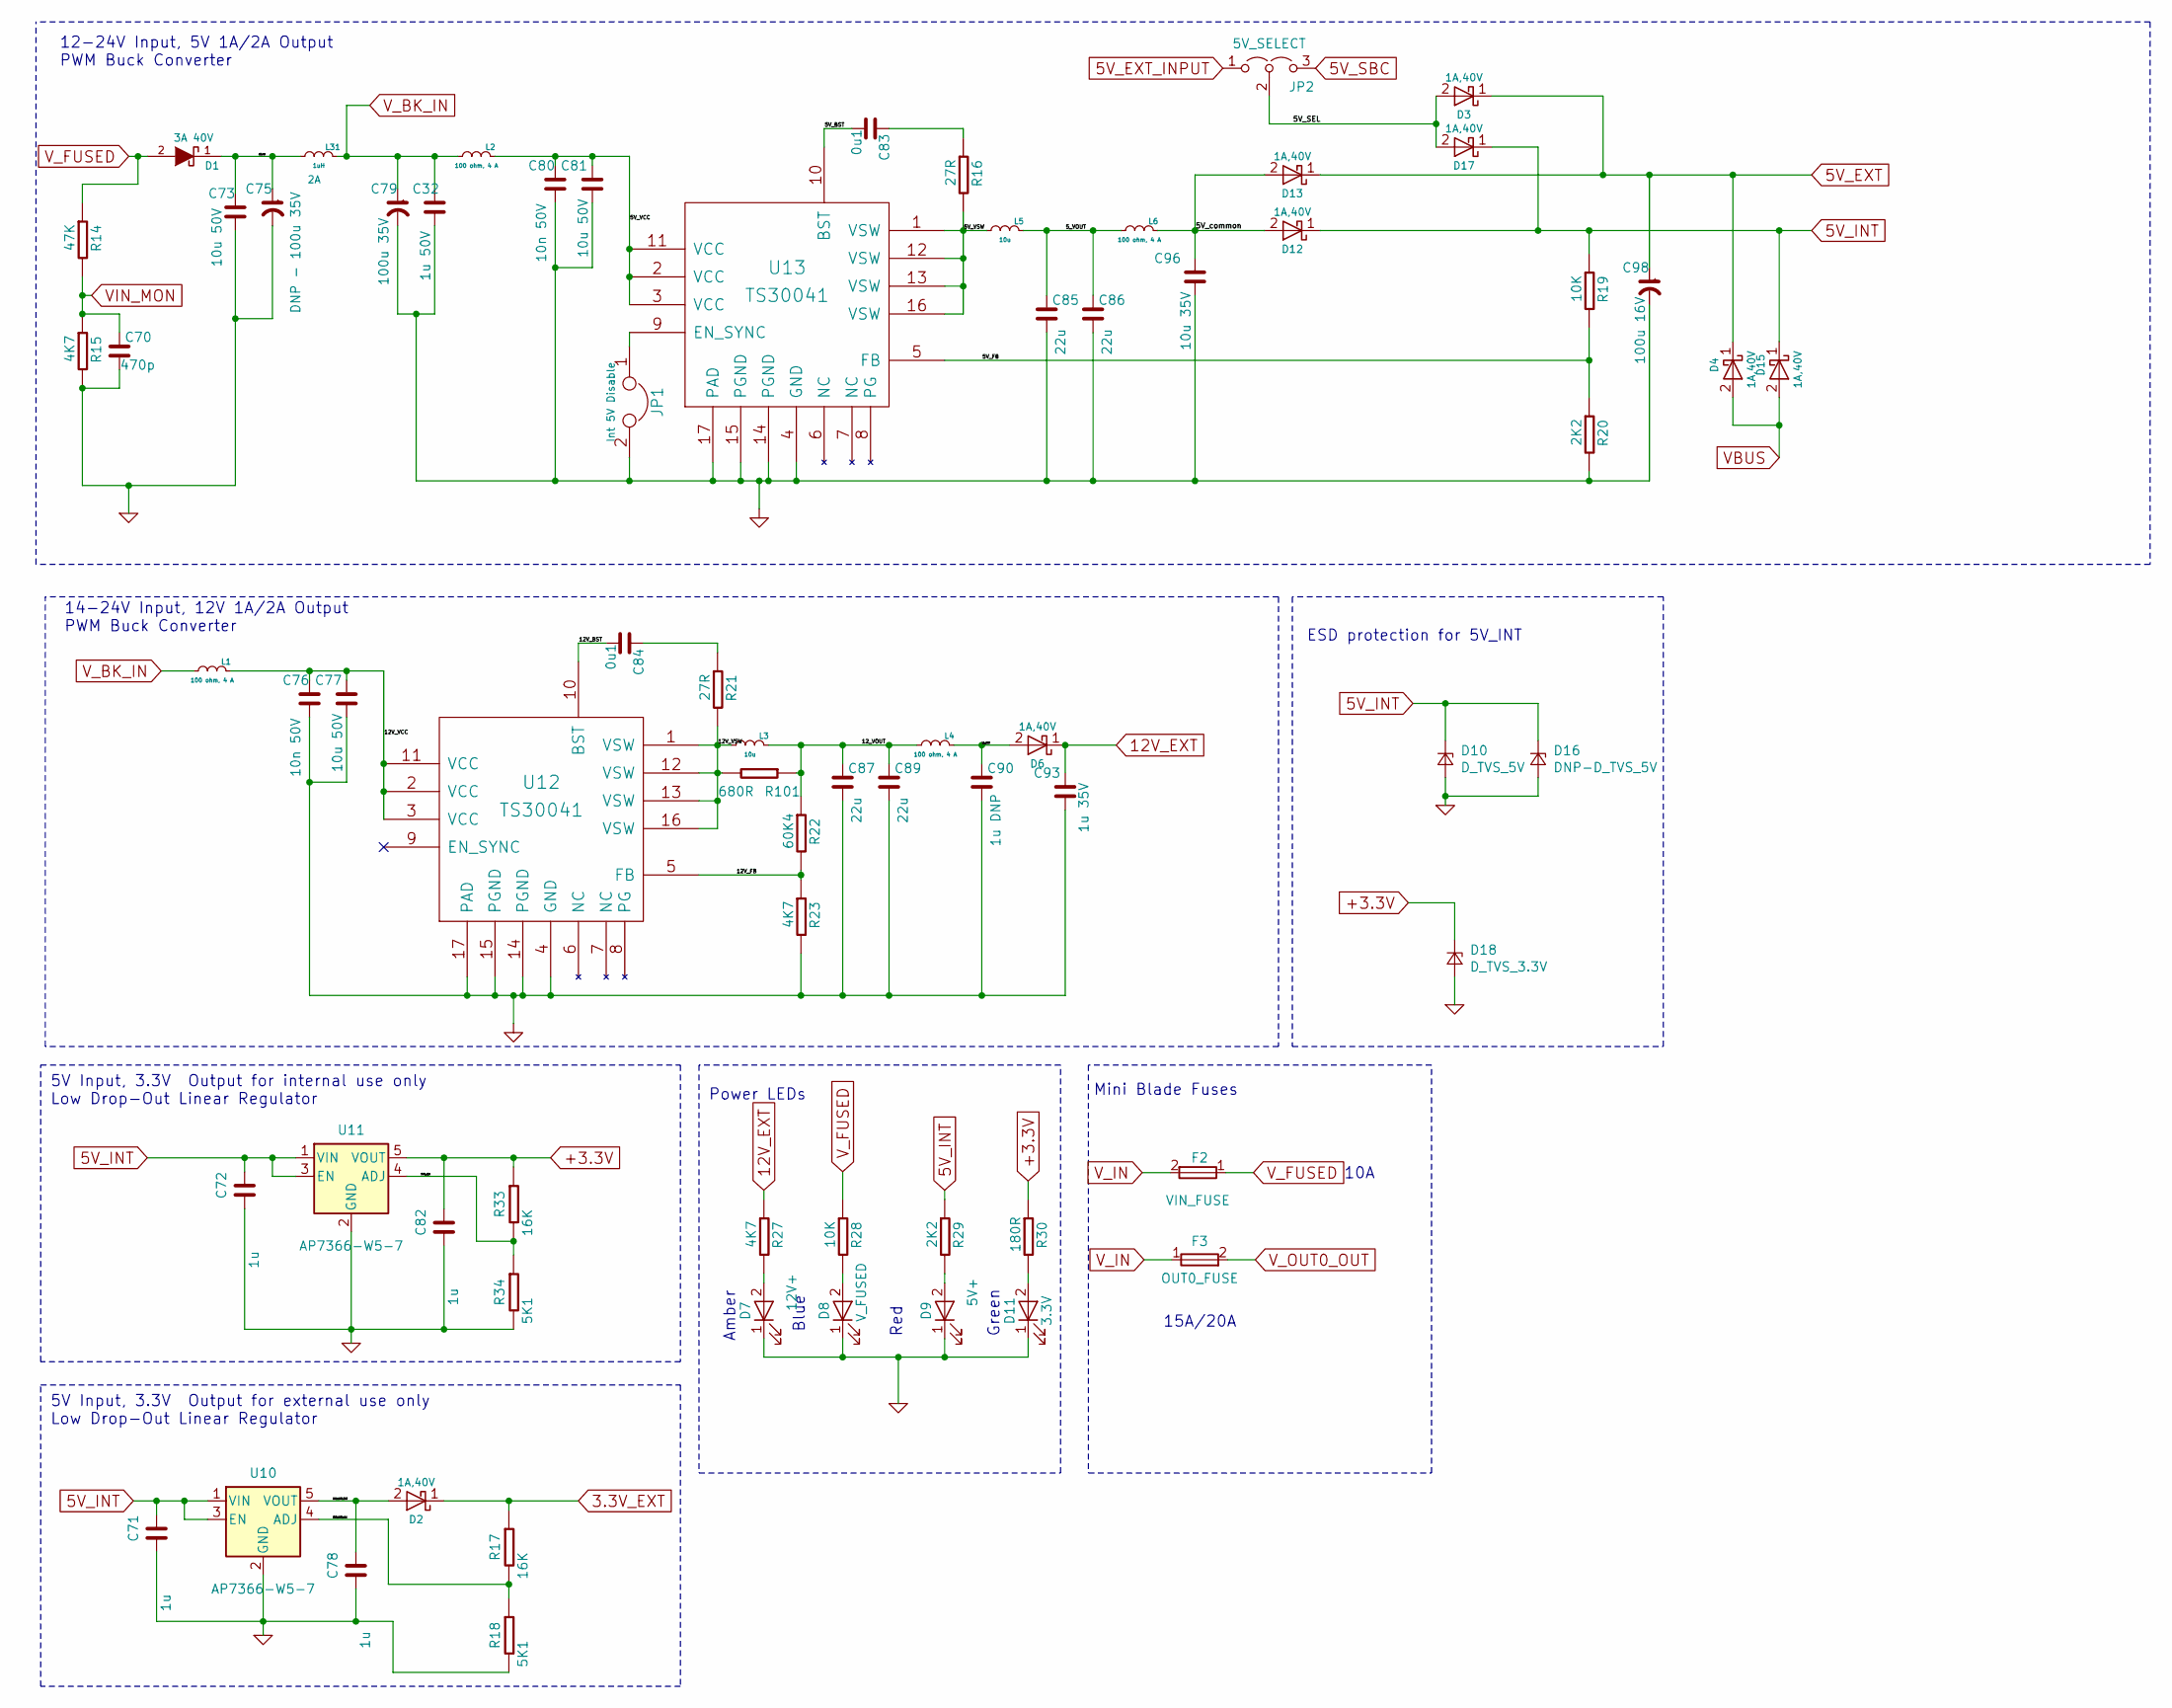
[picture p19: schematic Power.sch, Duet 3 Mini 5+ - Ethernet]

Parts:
C32: 1u 50V; C_0603_1608Metric_Wbry; Part Number CL10A105KB8NNNC
C70: 470p; C_0402_1005Metric_Wbry; Part Number CC0402KRX7R9BB471 or similar 10V+
C71, C72, C78, C82: 1u; C_0603_1608Metric_Wbry; Part Number CL10B105MO8NNWC or equivalent 16V+
C73, C77, C81: 10u 50V; C_1206_3216Metric; Part Number CL31A106MBHNNNE
C75: DNP - 100u 35V; CP_Elec_6.3x7.7; Part Number DNP e.g EEEFT1V101AP or 865080545012
C76: 10n 50V; C_0603_1608Metric_Wbry; Part Number CL10B103KB8NNNC
C79: 100u 35V; CP_Elec_6.3x7.7; Part Number e.g EEEFT1V101AP or 865080545012
C80: 10n 50V; C_0603_1608Metric_Wbry; Part Number CL10B103KB8NNNC or similar
C83, C84: 0u1; C_0402_1005Metric_Wbry; Part Number CL05A104KA5NNNC or similar
C85, C86, C87, C89: 22u; C_0805_2012Metric; Rating 25V; Part Number GRM21BR61E226ME44L
C90: 1u DNP; C_0603_1608Metric_Wbry; Rating 35V + DNP; Part Number CL10A105KB8NNNC or equivalent
C93: 1u 35V; C_0603_1608Metric_Wbry; Rating 35V +; Part Number CL10A105KB8NNNC or equivalent 35V+
C96: 10u 35V; C_1206_3216Metric; Part Number CL31A106KBHNNNE or similar 35V+
C98: 100u 16V; CP_Elec_6.3x7.7; Part Number 865080545012 or similar 16V+
D1: 3A 40V; D_SMA; Part Number ACDBA340-HF, SK34ATR or similar
D2, D3, D4, D6, D12, D13, D15, D17: 1A,40V; D_SOD-123F; Rating 1A,40V; Part Number DSS14UTR or RB162MM-40TR or similar
D7: 12V+; LED_0603_1608Metric; Part Number 150060AS75000 or equivalent Amber
D8: V_FUSED; LED_0603_1608Metric; Part Number 150060BS75000 or equivalent Blue
D9: 5V+; LED_0603_1608Metric; Part Number 150060RS75000 or equivalent Red
D10: D_TVS_5V; DFN1610-2L; Part Number 824032815 or 824031815 (DNP if D16 is p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
D11: 3.3V; LED_0603_1608Metric; Part Number 150060VS75000 or equivalent Green
D16: DNP-D_TVS_5V; D_SMC; Part Number SMCJ5.0A (DNP if D10 is populated)
D18: D_TVS_3.3V; DFN1610-2L; Part Number 824032813
F2: VIN_FUSE; MCCQ-122-minibladefuseholder; Part Number MCCQ-122 + 10A fuse
F3: OUT0_FUSE; MCCQ-122-minibladefuseholder; Part Number MCCQ-122 +15A fuse
JP1: Int 5V Disable; PinHeader_1x02_P2.54mm_Vertical; Part Number THS-02-R
JP2: 5V_SELECT; PinHeader_1x03_P2.54mm_Vertical; Part Number THS-03-R
L1, L2, L4, L6: 100 ohm, 4 A; L_0805_2012Metric; Part Number MPZ2012S101A or similar
L3, L5: 10u; L_Wuerth_7440405xxxx; Part Number 74404054100 or NR5040T100M
L31: 1uH; L_0806_2016Metric; Rating 2A; Part Number BDCD002016101R0MS1 or MAKK2016T1R0M
R14: 47K; R_0402_1005Metric_Wbry; Part Number RMCF0402FT47K0
R15, R23, R27: 4K7; R_0402_1005Metric_Wbry; Part Number RK73H1ETTP4701F
R16, R21: 27R; R_0402_1005Metric_Wbry; Rating 0.1W+; Part Number RK73H1ETTP10R0F
R17, R33: 16K; R_0402_1005Metric_Wbry; Part Number RMCF0402FT16K0
R18, R34: 5K1; R_0402_1005Metric_Wbry; Part Number ERJ3EKF5101V
R19, R28: 10K; R_0402_1005Metric_Wbry; Part Number RK73H1ETTP1002F
R20, R29: 2K2; R_0402_1005Metric_Wbry; Part Number RK73H1ETTP2201F
R22: 60K4; R_0402_1005Metric_Wbry; Part Number ERJ-2RKF6042X
R30: 180R; R_0402_1005Metric_Wbry; Part Number RMCF0402FT180R
R101: 680R; R_0805_2012Metric; Rating 0.5W; Part Number 680R 0.5W (ERJ-P06F6653V 665R is an alt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
U10, U11: AP7366-W5-7; SOT-23-5; Part Number AP7366-W5-7
U12, U13: TS30041; QFN-16-1EP_3x3mm_P0.5mm_EP1.8x1.8mm_ThermalVias; Part Number TS30041-M000QFNR

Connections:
3.3V_EXT: D2.1 (K), R17.1; also elsewhere on the board
5V_EXT: C98.1, D3.1 (K), D4.1 (K), D13.1 (K); also elsewhere on the board
5V_EXT_INPUT: JP2.1 (A); also elsewhere on the board
5V_INT: C71.1, C72.1, D10.1 (K), D12.1 (K), D15.1 (K), D16.1 (K), D17.1 (K), R19.1, R29.1, U10.1 (VIN), U10.3 (EN), U11.1 (VIN), U11.3 (EN); also elsewhere on the board
5V_SBC: JP2.3 (B); also elsewhere on the board
12V_EXT: C93.1, D6.1 (K), R27.1; also elsewhere on the board
+3.3V: C82.1, D18.1 (K), R30.1, R33.1, U11.5 (VOUT); also elsewhere on the board
/Power/3V3_ADJ: R33.2, R34.1, U11.4 (ADJ)
/Power/3V3_EXT_ADJ: R17.2, R18.1, U10.4 (ADJ)
/Power/3V3_EXT_OUT: C78.1, D2.2 (A), U10.5 (VOUT)
/Power/5V_BST: C83.2, U13.10 (BST)
/Power/5V_FB: R19.2, R20.1, U13.5 (FB)
/Power/5V_SEL: D3.2 (A), D17.2 (A), JP2.2 (C)
/Power/5V_VCC: C80.1, C81.1, L2.1 (A), U13.2 (VCC), U13.3 (VCC), U13.11 (VCC)
/Power/5V_VSW: L5.2 (B), R16.2, U13.1 (VSW), U13.12 (VSW), U13.13 (VSW), U13.16 (VSW)
/Power/5V_common: C96.1, D12.2 (A), D13.2 (A), L6.1 (A)
/Power/5_VOUT: C85.1, C86.1, L5.1 (A), L6.2 (B)
/Power/12V_BST: C84.2, U12.10 (BST)
/Power/12V_FB: R22.2, R23.1, U12.5 (FB)
/Power/12V_VCC: C76.1, C77.1, L1.1 (A), U12.2 (VCC), U12.3 (VCC), U12.11 (VCC)
/Power/12V_VSW: L3.2 (B), R21.2, R101.2, U12.1 (VSW), U12.12 (VSW), U12.13 (VSW), U12.16 (VSW)
/Power/12_VOUT: C87.1, C89.1, L3.1 (A), L4.2 (B), R22.1, R101.1
/Power/L4_OUT: C90.1, D6.2 (A), L4.1 (A)
/Power/d1out: C73.1, C75.1, D1.1 (K), L31.2 (B)
GND: C32.2, C70.2, C71.2, C72.2, C73.2, C75.2, C76.2, C77.2, C78.2, C79.2, C80.2, C81.2, C82.2, C85.2, C86.2, C87.2, C89.2, C90.2, C93.2, C96.2, C98.2, D7.1 (K), D8.1 (K), D9.1 (K), D10.2 (A), D11.1 (K), D16.2 (A), D18.2 (A), JP1.2, R15.2, R18.2, R20.2, R23.2, R34.2, U10.2 (GND), U11.2 (GND), U12.4 (GND), U12.14 (PGND), U12.15 (PGND), U12.17 (PAD), U13.4 (GND), U13.14 (PGND), U13.15 (PGND), U13.17 (PAD); also elsewhere on the board
unnamed: C83.1, R16.1
unnamed: C84.1, R21.1
unnamed: D7.2 (A), R27.2
unnamed: D8.2 (A), R28.2
unnamed: D9.2 (A), R29.2
unnamed: D11.2 (A), R30.2
unnamed: JP1.1, U13.9 (EN_SYNC)
VBUS: D4.2 (A), D15.2 (A); also elsewhere on the board
VIN_MON: C70.1, R14.2, R15.1; also elsewhere on the board
V_BK_IN: C32.1, C79.1, L1.2 (B), L2.2 (B), L31.1 (A)
V_FUSED: D1.2 (A), F2.1, R14.1, R28.1; also elsewhere on the board
V_IN: F2.2, F3.1; also elsewhere on the board
V_OUT0_OUT: F3.2; also elsewhere on the board

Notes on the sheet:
Mini Blade Fuses
5V Input, 3.3V Output for internal use only Low Drop-Out Linear Regulator
Power LEDs
Blue
Red
Green
10A
15A/20A
5V Input, 3.3V Output for external use only Low Drop-Out Linear Regulator
14-24V Input, 12V 1A/2A Output PWM Buck Converter
Amber
ESD protection for 5V_INT
12-24V Input, 5V 1A/2A Output PWM Buck Converter

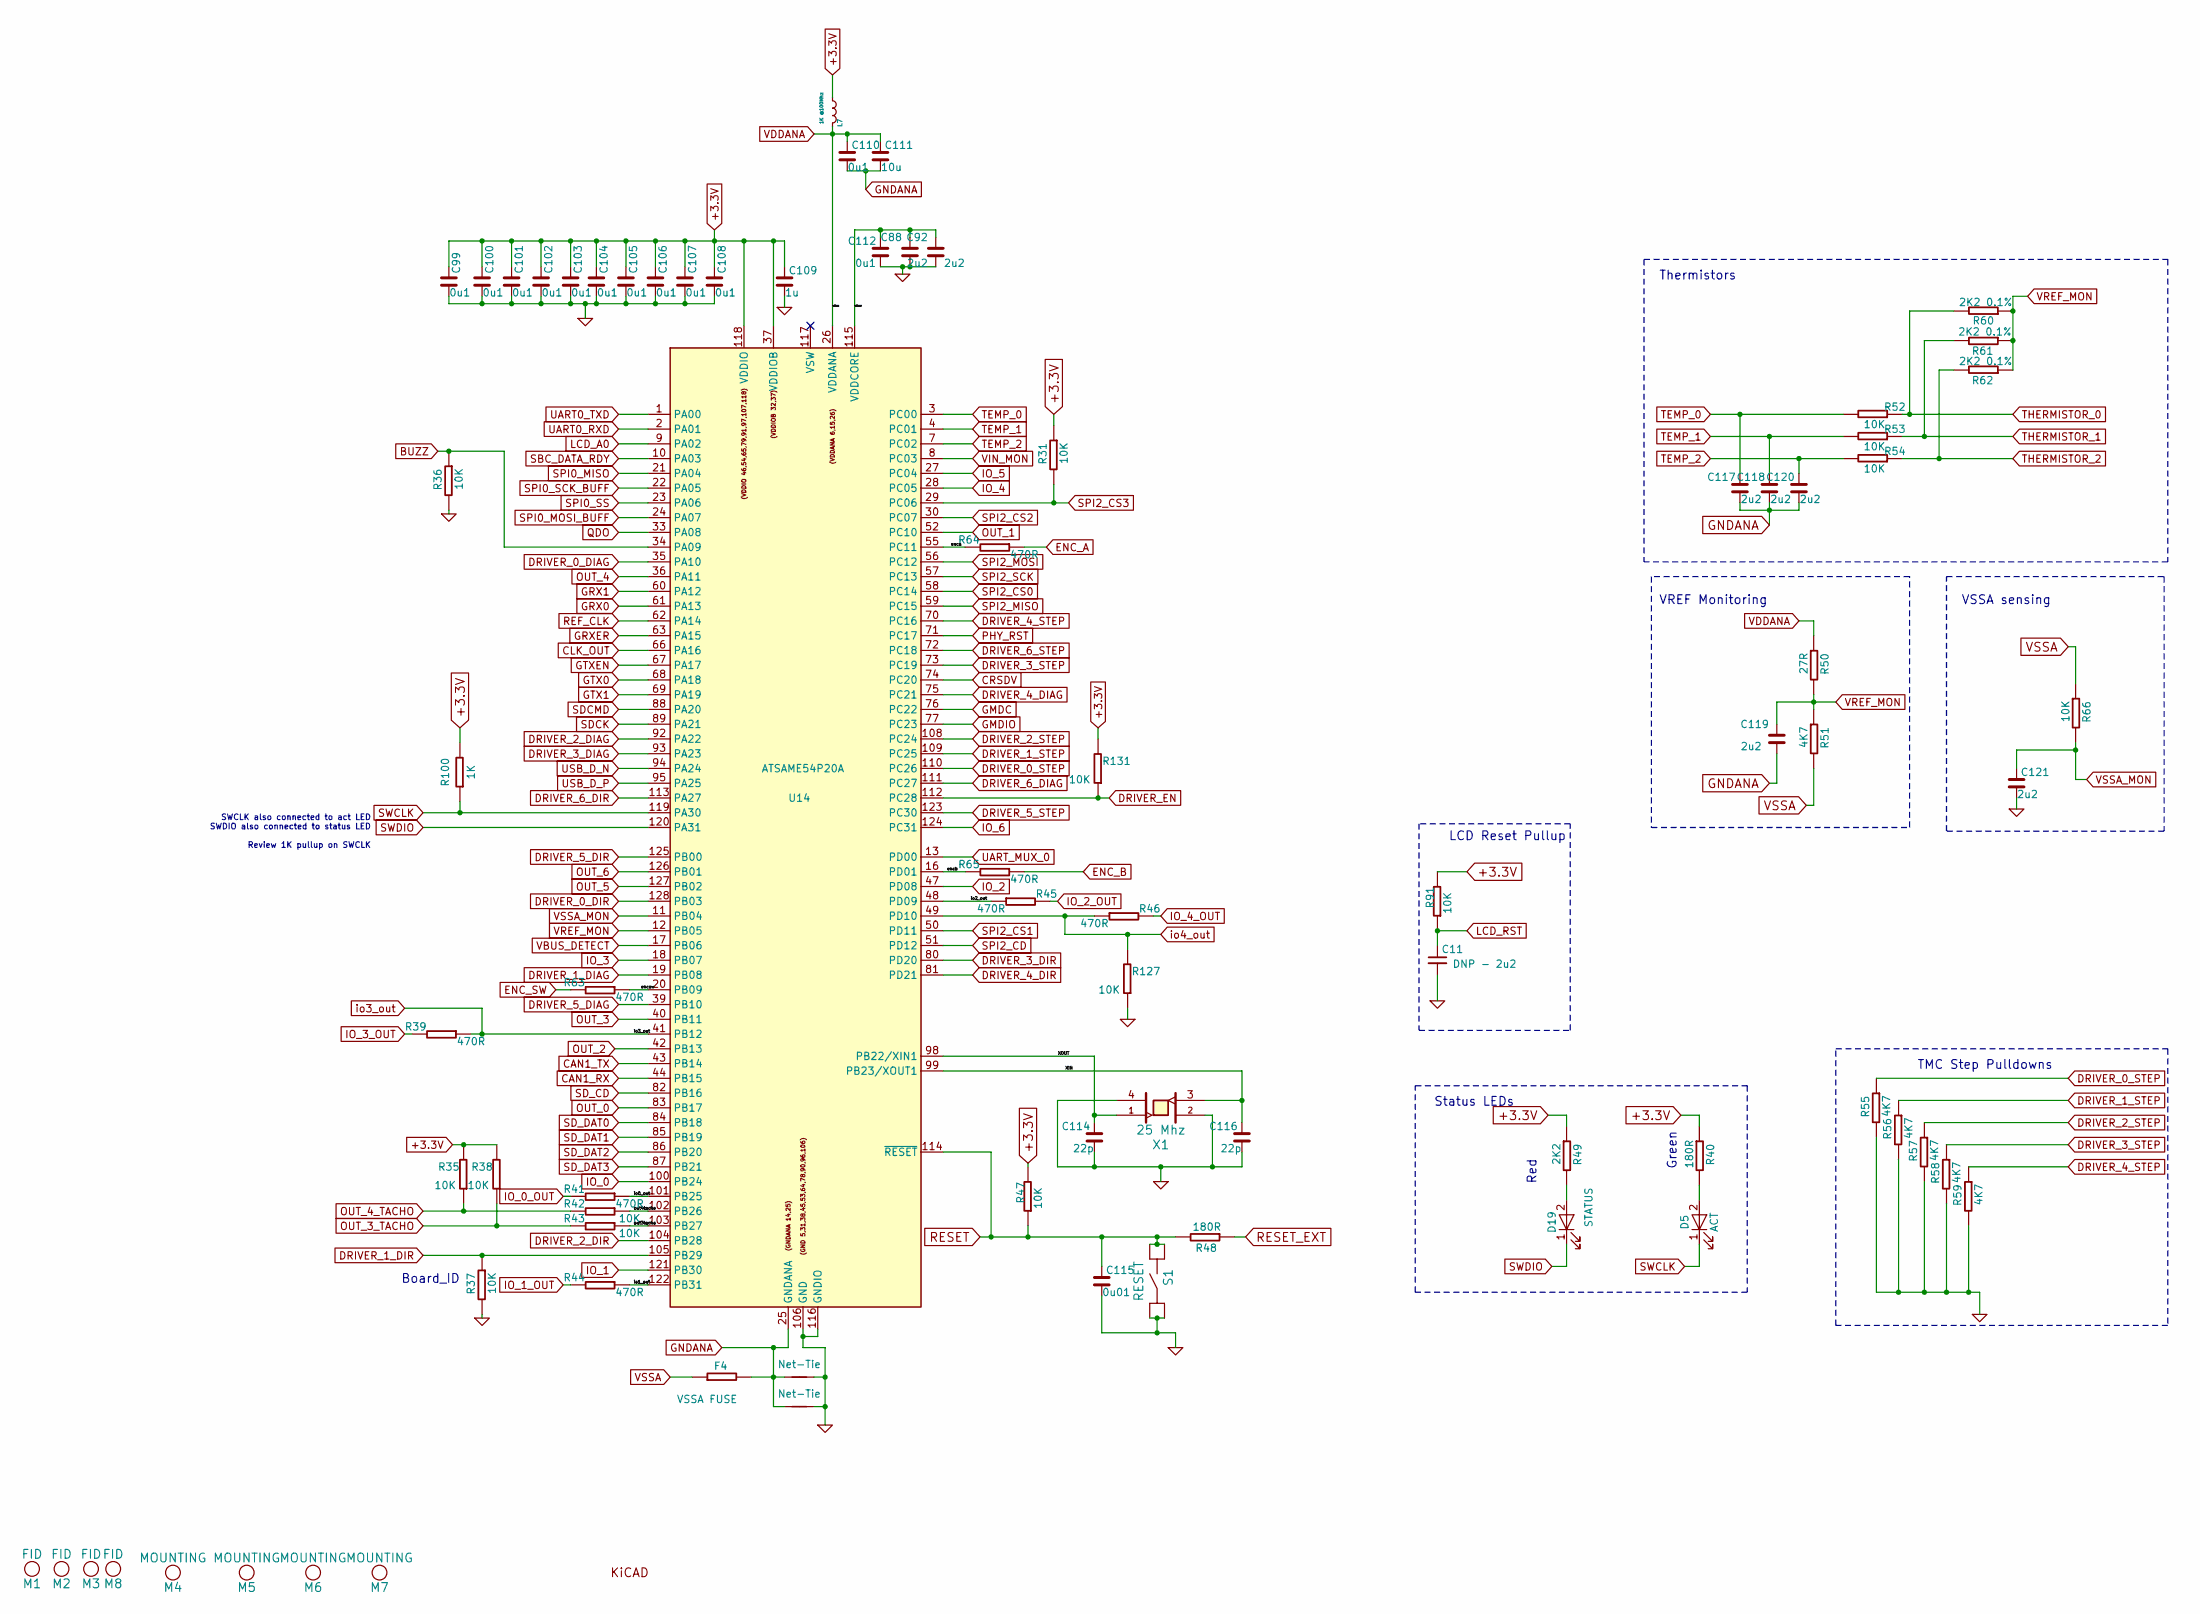
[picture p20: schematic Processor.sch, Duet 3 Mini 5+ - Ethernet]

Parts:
C11: DNP - 2u2; C_0402_1005Metric_Wbry; Part Number DNP - LMK105BJ225KV-F or similar 10v+
C88, C92, C117, C118, C119, C120, C121: 2u2; C_0402_1005Metric_Wbry; Part Number LMK105BJ225KV-F or similar 10v+
C99, C100, C101, C102, C103, C104, C105, C106, C107, C108, C110, C112: 0u1; C_0402_1005Metric_Wbry; Part Number CL05A104KA5NNNC or similar
C109: 1u; C_0603_1608Metric_Wbry; Part Number CL10B105MO8NNWC or equivalent 16V+
C111: 10u; C_0805_2012Metric; Part Number e.g CL21A106KQCLRNC
C114, C116: 22p; C_0402_1005Metric_Wbry; Part Number C0402C220J4GACTU
C115: 0u01; C_0402_1005Metric_Wbry; Part Number TMK105B7103KV-F
D5: ACT; LED_0603_1608Metric; Part Number 150060VS75000 or equivalent Green
D19: STATUS; LED_0603_1608Metric; Part Number 150060RS75000 or equivalent Red
F4: VSSA FUSE; Fuse_1206_3216Metric; Part Number 0ZCJ0020FF2E
L7: 1K @100Mhz; L_0603_1608Metric; Part Number BK1608HS102-T or PE-0603FB102ST or simi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
M1, M2, M3, M8: FID; Fiducial_1mm_Mask2mm; Part Number DNP - Virtual component
M4, M5, M6, M7: MOUNTING; MountingHole_4.3mm_M4; Part Number DNP - Virtual component
M12: Logo_KICAD; KiCad-Logo_6mm_SilkScreen; Part Number DNP - Virtual component
NT1, NT2: Net-Tie; NetTie-2_SMD_Pad0.5mm; Part Number DNP - Virtual component
R31, R35, R36, R37, R38, R42, R43, R47, R52, R53, R54, R66, R91, R127, R131: 10K; R_0402_1005Metric_Wbry; Part Number RK73H1ETTP1002F
R39, R41, R44, R45, R46, R63, R64, R65: 470R; R_0402_1005Metric_Wbry; Part Number RK73H1ETTP4700F
R40, R48: 180R; R_0402_1005Metric_Wbry; Part Number RMCF0402FT180R
R49: 2K2; R_0402_1005Metric_Wbry; Part Number RK73H1ETTP2201F
R50: 27R; R_0402_1005Metric_Wbry; Part Number RC0402FR-0727RL
R51, R55, R56, R57, R58, R59: 4K7; R_0402_1005Metric_Wbry; Part Number RK73H1ETTP4701F
R60, R61, R62: 2K2 0.1%; R_0402_1005Metric_Wbry; Part Number RT0402BRE072K2L
R100: 1K; R_0402_1005Metric_Wbry; Part Number RK73H1ETTP1001F
S1: RESET; SW_SIDE_1_lugs; Part Number LY-A03-02A
U14: ATSAME54P20A; TQFP-128_14x14mm_P0.4mm; Part Number ATSAME54P20A
X1: TSX-3225 25.0000MF10P; Crystal_SMD_ECS-33B-4Pin_3.2x2.5mm; Part Number TSX-3225 25.0000MF10P

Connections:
+3.3V: C99.1, C100.1, C101.1, C102.1, C103.1, C104.1, C105.1, C106.1, C107.1, C108.1, C109.1, L7.2 (B), R31.1, R35.2, R38.2, R40.1, R47.2, R49.1, R91.2, R100.2, R131.2, U14.32 (VDDIOB), U14.37 (VDDIOB), U14.46 (VDDIO), U14.54 (VDDIO), U14.65 (VDDIO), U14.79 (VDDIO), U14.91 (VDDIO), U14.97 (VDDIO), U14.107 (VDDIO), U14.118 (VDDIO); also elsewhere on the board
/Processor/XIN: C116.1, U14.99 (PB23/XOUT1), X1.3
/Processor/XOUT: C114.1, U14.98 (PB22/XIN1), X1.1
/Processor/enca: R64.2, U14.55 (PC11)
/Processor/encb: R65.2, U14.16 (PD01)
/Processor/encsw: R63.1, U14.20 (PB09)
/Processor/io0_out: R41.1, U14.101 (PB25)
/Processor/io1_out: R44.1, U14.122 (PB31)
/Processor/io2_out: R45.1, U14.48 (PD09)
/Processor/out3tacho: R43.1, U14.103 (PB27)
/Processor/out4tacho: R42.1, U14.102 (PB26)
/Processor/vddcore: C88.1, C92.1, C112.1, U14.115 (VDDCORE)
BUZZ: R36.1, U14.34 (PA09); also elsewhere on the board
CAN1_RX: U14.44 (PB15); also elsewhere on the board
CAN1_TX: U14.43 (PB14); also elsewhere on the board
CLK_OUT: U14.66 (PA16); also elsewhere on the board
CRSDV: U14.74 (PC20); also elsewhere on the board
DRIVER_0_DIAG: U14.35 (PA10); also elsewhere on the board
DRIVER_0_DIR: U14.128 (PB03); also elsewhere on the board
DRIVER_0_STEP: R55.1, U14.110 (PC26); also elsewhere on the board
DRIVER_1_DIAG: U14.19 (PB08); also elsewhere on the board
DRIVER_1_DIR: R37.1, U14.105 (PB29); also elsewhere on the board
DRIVER_1_STEP: R56.1, U14.109 (PC25); also elsewhere on the board
DRIVER_2_DIAG: U14.92 (PA22); also elsewhere on the board
DRIVER_2_DIR: U14.104 (PB28); also elsewhere on the board
DRIVER_2_STEP: R57.1, U14.108 (PC24); also elsewhere on the board
DRIVER_3_DIAG: U14.93 (PA23); also elsewhere on the board
DRIVER_3_DIR: U14.80 (PD20); also elsewhere on the board
DRIVER_3_STEP: R58.1, U14.73 (PC19); also elsewhere on the board
DRIVER_4_DIAG: U14.75 (PC21); also elsewhere on the board
DRIVER_4_DIR: U14.81 (PD21); also elsewhere on the board
DRIVER_4_STEP: R59.1, U14.70 (PC16); also elsewhere on the board
DRIVER_5_DIAG: U14.39 (PB10); also elsewhere on the board
DRIVER_5_DIR: U14.125 (PB00); also elsewhere on the board
DRIVER_5_STEP: U14.123 (PC30); also elsewhere on the board
DRIVER_6_DIAG: U14.111 (PC27); also elsewhere on the board
DRIVER_6_DIR: U14.113 (PA27); also elsewhere on the board
DRIVER_6_STEP: U14.72 (PC18); also elsewhere on the board
DRIVER_EN: R131.1, U14.112 (PC28); also elsewhere on the board
ENC_A: R64.1; also elsewhere on the board
ENC_B: R65.1; also elsewhere on the board
ENC_SW: R63.2; also elsewhere on the board
GMDC: U14.76 (PC22); also elsewhere on the board
GMDIO: U14.77 (PC23); also elsewhere on the board
GND: C11.2, C88.2, C92.2, C99.2, C100.2, C101.2, C102.2, C103.2, C104.2, C105.2, C106.2, C107.2, C108.2, C109.2, C112.2, C114.2, C115.2, C116.2, C121.2, NT1.2, NT2.2, R36.2, R37.2, R55.2, R56.2, R57.2, R58.2, R59.2, R127.1, S1.1, S1.2, U14.5 (GND), U14.31 (GND), U14.38 (GND), U14.45 (GND), U14.53 (GND), U14.64 (GND), U14.78 (GND), U14.90 (GND), U14.96 (GND), U14.106 (GND), U14.116 (GNDIO), X1.2, X1.4; also elsewhere on the board
GNDANA: C110.2, C111.2, C117.2, C118.2, C119.2, C120.2, F4.2, NT1.1, NT2.1, U14.14 (GNDANA), U14.25 (GNDANA)
GRX0: U14.61 (PA13); also elsewhere on the board
GRX1: U14.60 (PA12); also elsewhere on the board
GRXER: U14.63 (PA15); also elsewhere on the board
GTX0: U14.68 (PA18); also elsewhere on the board
GTX1: U14.69 (PA19); also elsewhere on the board
GTXEN: U14.67 (PA17); also elsewhere on the board
IO_0: U14.100 (PB24); also elsewhere on the board
IO_0_OUT: R41.2; also elsewhere on the board
IO_1: U14.121 (PB30); also elsewhere on the board
IO_1_OUT: R44.2; also elsewhere on the board
IO_2: U14.47 (PD08); also elsewhere on the board
IO_2_OUT: R45.2; also elsewhere on the board
IO_3: U14.18 (PB07); also elsewhere on the board
IO_3_OUT: R39.2; also elsewhere on the board
IO_4: U14.28 (PC05); also elsewhere on the board
IO_4_OUT: R46.2; also elsewhere on the board
IO_5: U14.27 (PC04); also elsewhere on the board
IO_6: U14.124 (PC31); also elsewhere on the board
LCD_A0: U14.9 (PA02); also elsewhere on the board
LCD_RST: C11.1, R91.1; also elsewhere on the board
unnamed: D5.2 (A), R40.2
unnamed: D19.2 (A), R49.2
OUT_0: U14.83 (PB17); also elsewhere on the board
OUT_1: U14.52 (PC10); also elsewhere on the board
OUT_2: U14.42 (PB13); also elsewhere on the board
OUT_3: U14.40 (PB11); also elsewhere on the board
OUT_3_TACHO: R38.1, R43.2; also elsewhere on the board
OUT_4: U14.36 (PA11); also elsewhere on the board
OUT_4_TACHO: R35.1, R42.2; also elsewhere on the board
OUT_5: U14.127 (PB02); also elsewhere on the board
OUT_6: U14.126 (PB01); also elsewhere on the board
PHY_RST: U14.71 (PC17); also elsewhere on the board
QDO: U14.33 (PA08); also elsewhere on the board
REF_CLK: U14.62 (PA14); also elsewhere on the board
RESET: C115.1, R47.1, R48.2, S1.3, S1.4, U14.114 (~RESET); also elsewhere on the board
RESET_EXT: R48.1; also elsewhere on the board
SBC_DATA_RDY: U14.10 (PA03); also elsewhere on the board
SDCK: U14.89 (PA21); also elsewhere on the board
SDCMD: U14.88 (PA20); also elsewhere on the board
SD_CD: U14.82 (PB16); also elsewhere on the board
SD_DAT0: U14.84 (PB18); also elsewhere on the board
SD_DAT1: U14.85 (PB19); also elsewhere on the board
SD_DAT2: U14.86 (PB20); also elsewhere on the board
SD_DAT3: U14.87 (PB21); also elsewhere on the board
SPI0_MISO: U14.21 (PA04); also elsewhere on the board
SPI0_MOSI_BUFF: U14.24 (PA07); also elsewhere on the board
SPI0_SCK_BUFF: U14.22 (PA05); also elsewhere on the board
SPI0_SS: U14.23 (PA06); also elsewhere on the board
SPI2_CD: U14.51 (PD12); also elsewhere on the board
SPI2_CS0: U14.58 (PC14); also elsewhere on the board
SPI2_CS1: U14.50 (PD11); also elsewhere on the board
SPI2_CS2: U14.30 (PC07); also elsewhere on the board
SPI2_CS3: R31.2, U14.29 (PC06); also elsewhere on the board
SPI2_MISO: U14.59 (PC15); also elsewhere on the board
SPI2_MOSI: U14.56 (PC12); also elsewhere on the board
SPI2_SCK: U14.57 (PC13); also elsewhere on the board
SWCLK: D5.1 (K), R100.1, U14.119 (PA30); also elsewhere on the board
SWDIO: D19.1 (K), U14.120 (PA31); also elsewhere on the board
TEMP_0: C117.1, R52.2, U14.3 (PC00)
TEMP_1: C118.1, R53.2, U14.4 (PC01)
TEMP_2: C120.1, R54.2, U14.7 (PC02)
THERMISTOR_0: R52.1, R60.2; also elsewhere on the board
THERMISTOR_1: R53.1, R61.2; also elsewhere on the board
THERMISTOR_2: R54.1, R62.2; also elsewhere on the board
UART0_RXD: U14.2 (PA01); also elsewhere on the board
UART0_TXD: U14.1 (PA00); also elsewhere on the board
UART_MUX_0: U14.13 (PD00); also elsewhere on the board
USB_D_N: U14.94 (PA24); also elsewhere on the board
USB_D_P: U14.95 (PA25); also elsewhere on the board
VBUS_DETECT: U14.17 (PB06); also elsewhere on the board
VDDANA: C110.1, C111.1, L7.1 (A), R50.1, U14.6 (VDDANA), U14.15 (VDDANA), U14.26 (VDDANA)
VIN_MON: U14.8 (PC03); also elsewhere on the board
VREF_MON: C119.1, R50.2, R51.1, R60.1, R61.1, R62.1, U14.12 (PB05)
VSSA: F4.1, R51.2, R66.1; also elsewhere on the board
VSSA_MON: C121.1, R66.2, U14.11 (PB04)
io3_out: R39.1, U14.41 (PB12); also elsewhere on the board
io4_out: R46.1, R127.2, U14.49 (PD10); also elsewhere on the board

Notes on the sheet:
VSSA sensing
Red
Status LEDs
TMC Step Pulldowns
Thermistors
VREF Monitoring
SWCLK also connected to act LED SWDIO also connected to status LED Review 1K pullup on SWCLK
Board_ID
LCD Reset Pullup
Green

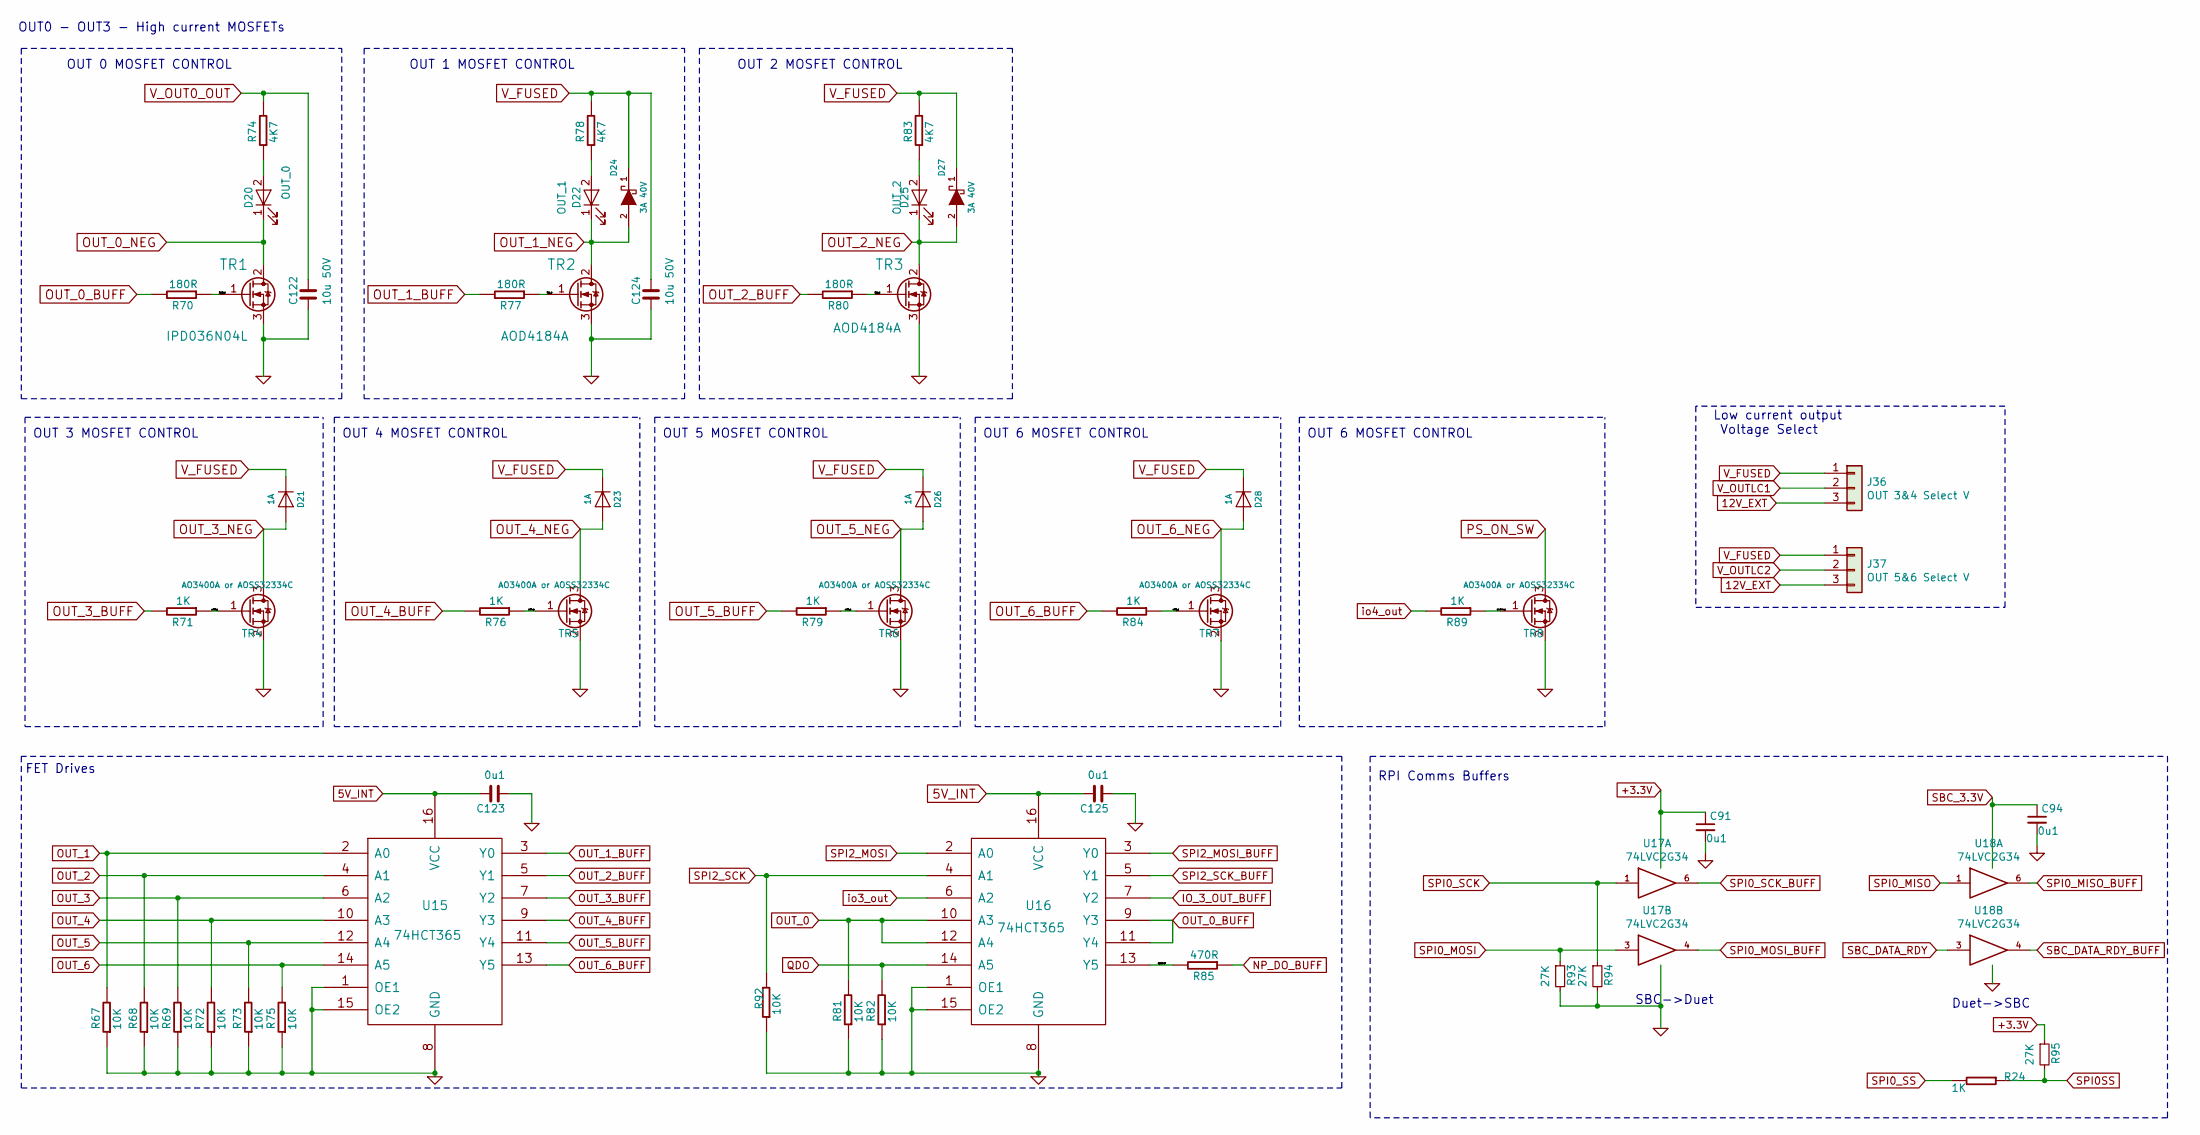
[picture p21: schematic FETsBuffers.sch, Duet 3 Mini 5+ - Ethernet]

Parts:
C91, C94, C123, C125: 0u1; C_0402_1005Metric_Wbry; Part Number CL05A104KA5NNNC or similar
C122, C124: 10u 50V; C_1206_3216Metric; Part Number CL31A106MBHNNNE
D20: OUT_0; LED_0603_1608Metric; Part Number 150060RS75000 or equivalent Red
D21, D23, D26, D28: 1A; D_SOD-123F; Part Number HS1KFL or equivalent
D22: OUT_1; LED_0603_1608Metric; Part Number 150060RS75000 or equivalent Red
D24, D27: 3A 40V; D_SMA; Part Number ACDBA340-HF, SK34ATR or similar
D25: OUT_2; LED_0603_1608Metric; Part Number 150060RS75000 or equivalent Red
J36: OUT 3&4 Select V; PinHeader_1x03_P2.54mm_Vertical; Part Number THS-03-R
J37: OUT 5&6 Select V; PinHeader_1x03_P2.54mm_Vertical; Part Number THS-03-RT
R24, R71, R76, R79, R84, R89: 1K; R_0402_1005Metric_Wbry; Part Number RK73H1ETTP1001F
R67, R68, R69, R72, R73, R75, R81, R82, R92: 10K; R_0402_1005Metric_Wbry; Part Number RK73H1ETTP1002F
R70, R77, R80: 180R; R_0402_1005Metric_Wbry; Part Number RMCF0402FT180R
R74, R78, R83: 4K7; R_0402_1005Metric_Wbry; Part Number RK73H1ETTP4701F
R85: 470R; R_0402_1005Metric_Wbry; Part Number RK73H1ETTP4700F
R93, R94, R95: 27K; R_0402_1005Metric_Wbry; Part Number RK73H1ETTP2702F
TR1: IPD036N04L; TO-252-2_vias; Part Number IPD90N04S4L04ATMA1
TR2, TR3: AOD4184A; TO-252-2_vias; Part Number AOD4184A
TR4, TR5, TR6, TR7, TR8: AO3400A; SOT-23_AO3400A; Part Number AO3400A or AOSS32334C
U15, U16: 74HCT365; TSSOP-16_4.4x5mm_P0.65mm; Part Number MC74HCT365ADTR2G or equivalent
U17, U18: 74LVC2G34; SOT-363_SC-70-6; Part Number 74LVC2G34GW,125

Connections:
5V_INT: C123.1, C125.1, U15.16 (VCC), U16.16 (VCC); also elsewhere on the board
12V_EXT: J36.3, J37.3; also elsewhere on the board
+3.3V: C91.1, R95.1, U17.5; also elsewhere on the board
/MOSFETs and Buffers/TR1_G: R77.1, TR2.1 (G)
/MOSFETs and Buffers/TR3_G: R80.1, TR3.1 (G)
/MOSFETs and Buffers/TR10_G: R70.1, TR1.1 (G)
/MOSFETs and Buffers/npdobuff: R85.2, U16.13 (Y5)
/MOSFETs and Buffers/out3_g: R71.1, TR4.1 (G)
/MOSFETs and Buffers/out4_g: R76.1, TR5.1 (G)
/MOSFETs and Buffers/out5_g: R79.1, TR6.1 (G)
/MOSFETs and Buffers/out6_g: R84.1, TR7.1 (G)
/MOSFETs and Buffers/psonsw_g: R89.1, TR8.1 (G)
GND: C91.2, C94.2, C122.2, C123.2, C124.2, C125.2, R67.1, R68.1, R69.1, R72.1, R73.1, R75.1, R81.1, R82.1, R92.1, R93.2, R94.2, TR1.3 (S), TR2.3 (S), TR3.3 (S), TR4.2 (S), TR5.2 (S), TR6.2 (S), TR7.2 (S), TR8.2 (S), U15.1 (OE1), U15.8 (GND), U15.15 (OE2), U16.1 (OE1), U16.8 (GND), U16.15 (OE2), U17.2 (GND), U18.2 (GND); also elsewhere on the board
IO_3_OUT_BUFF: U16.7 (Y2); also elsewhere on the board
NP_DO_BUFF: R85.1; also elsewhere on the board
unnamed: D20.2 (A), R74.1
unnamed: D22.2 (A), R78.1
unnamed: D25.2 (A), R83.1
OUT_0: R81.2, U16.10 (A3), U16.12 (A4); also elsewhere on the board
OUT_0_BUFF: R70.2, U16.9 (Y3), U16.11 (Y4)
OUT_0_NEG: D20.1 (K), TR1.2 (D); also elsewhere on the board
OUT_1: R67.2, U15.2 (A0); also elsewhere on the board
OUT_1_BUFF: R77.2, U15.3 (Y0)
OUT_1_NEG: D22.1 (K), D24.2 (A), TR2.2 (D); also elsewhere on the board
OUT_2: R68.2, U15.4 (A1); also elsewhere on the board
OUT_2_BUFF: R80.2, U15.5 (Y1)
OUT_2_NEG: D25.1 (K), D27.2 (A), TR3.2 (D); also elsewhere on the board
OUT_3: R69.2, U15.6 (A2); also elsewhere on the board
OUT_3_BUFF: R71.2, U15.7 (Y2)
OUT_3_NEG: D21.2 (A), TR4.3 (D); also elsewhere on the board
OUT_4: R72.2, U15.10 (A3); also elsewhere on the board
OUT_4_BUFF: R76.2, U15.9 (Y3)
OUT_4_NEG: D23.2 (A), TR5.3 (D); also elsewhere on the board
OUT_5: R73.2, U15.12 (A4); also elsewhere on the board
OUT_5_BUFF: R79.2, U15.11 (Y4)
OUT_5_NEG: D26.2 (A), TR6.3 (D); also elsewhere on the board
OUT_6: R75.2, U15.14 (A5); also elsewhere on the board
OUT_6_BUFF: R84.2, U15.13 (Y5); also elsewhere on the board
OUT_6_NEG: D28.2 (A), TR7.3 (D); also elsewhere on the board
PS_ON_SW: TR8.3 (D); also elsewhere on the board
QDO: R82.2, U16.14 (A5); also elsewhere on the board
SBC_3.3V: C94.1, U18.5; also elsewhere on the board
SBC_DATA_RDY: U18.3; also elsewhere on the board
SBC_DATA_RDY_BUFF: U18.4; also elsewhere on the board
SPI0SS: R24.1, R95.2; also elsewhere on the board
SPI0_MISO: U18.1; also elsewhere on the board
SPI0_MISO_BUFF: U18.6; also elsewhere on the board
SPI0_MOSI: R93.1, U17.3; also elsewhere on the board
SPI0_MOSI_BUFF: U17.4; also elsewhere on the board
SPI0_SCK: R94.1, U17.1; also elsewhere on the board
SPI0_SCK_BUFF: U17.6; also elsewhere on the board
SPI0_SS: R24.2; also elsewhere on the board
SPI2_MOSI: U16.2 (A0); also elsewhere on the board
SPI2_MOSI_BUFF: U16.3 (Y0); also elsewhere on the board
SPI2_SCK: R92.2, U16.4 (A1); also elsewhere on the board
SPI2_SCK_BUFF: U16.5 (Y1); also elsewhere on the board
V_FUSED: C124.1, D21.1 (K), D23.1 (K), D24.1 (K), D26.1 (K), D27.1 (K), D28.1 (K), J36.1, J37.1, R78.2, R83.2; also elsewhere on the board
V_OUT0_OUT: C122.1, R74.2; also elsewhere on the board
V_OUTLC1: J36.2; also elsewhere on the board
V_OUTLC2: J37.2; also elsewhere on the board
io3_out: U16.6 (A2); also elsewhere on the board
io4_out: R89.2; also elsewhere on the board

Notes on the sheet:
OUT 6 MOSFET CONTROL
FET Drives
OUT 3 MOSFET CONTROL
OUT 4 MOSFET CONTROL
OUT 5 MOSFET CONTROL
OUT 1 MOSFET CONTROL
OUT 2 MOSFET CONTROL
Low current output Voltage Select
OUT 0 MOSFET CONTROL
OUT0 - OUT3 - High current MOSFETs
SBC->Duet
Duet->SBC
RPI Comms Buffers

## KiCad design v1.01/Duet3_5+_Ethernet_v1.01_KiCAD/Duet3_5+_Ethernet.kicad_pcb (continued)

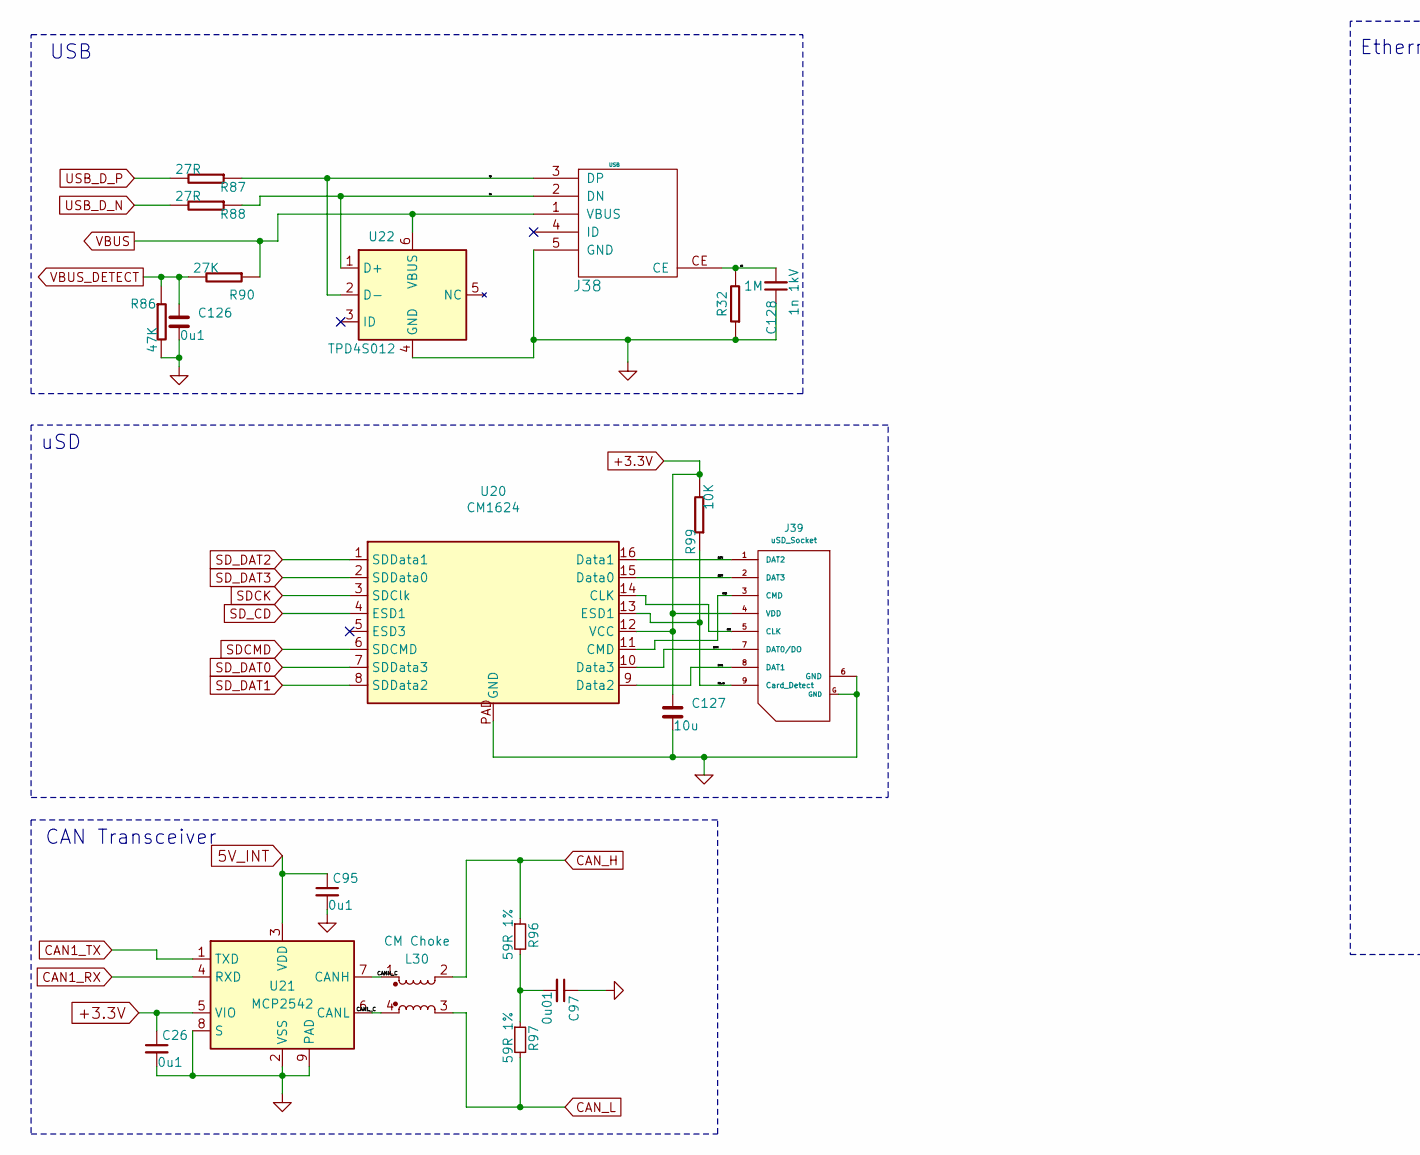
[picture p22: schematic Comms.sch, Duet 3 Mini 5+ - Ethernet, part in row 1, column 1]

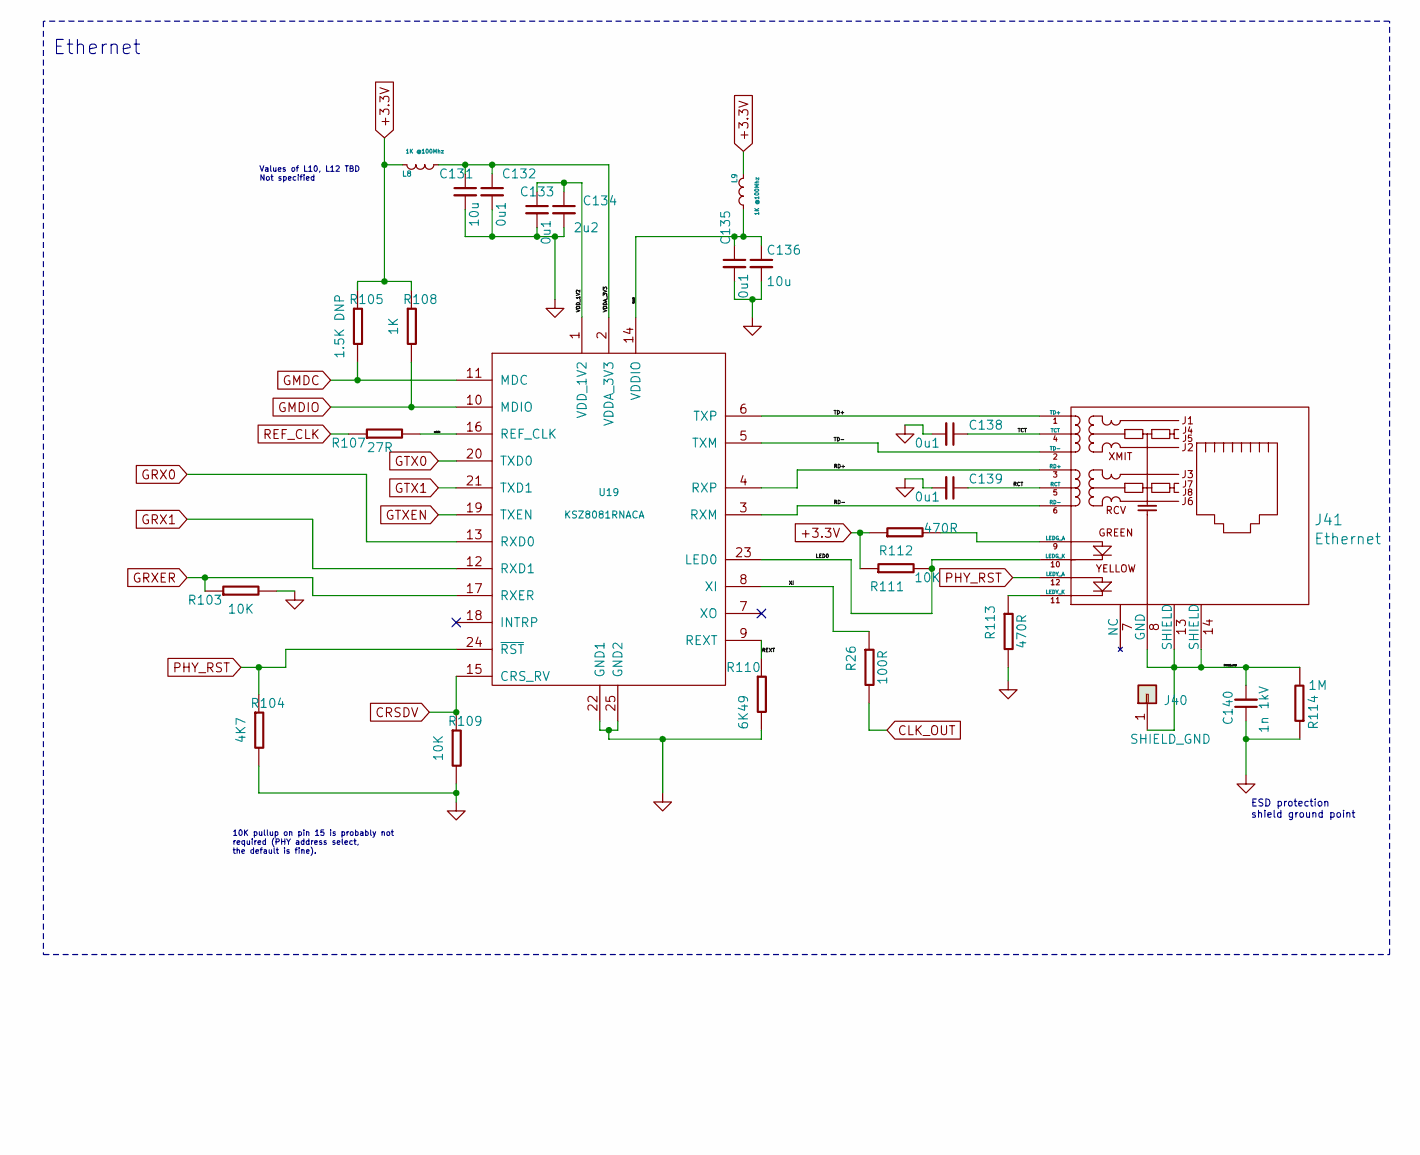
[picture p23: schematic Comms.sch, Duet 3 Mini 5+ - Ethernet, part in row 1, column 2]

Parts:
C26, C95, C126, C132, C133, C135, C138, C139: 0u1; C_0402_1005Metric_Wbry; Part Number CL05A104KA5NNNC or similar
C97: 0u01; C_0402_1005Metric_Wbry; Part Number TMK105B7103KV-F
C127, C131, C136: 10u; C_0805_2012Metric; Part Number e.g CL21A106KQCLRNC
C128, C140: 1n 1kV; C_0805_2012Metric; Part Number CC0805KRX7RCBB102
C134: 2u2; C_0402_1005Metric_Wbry; Part Number LMK105BJ225KV-F or similar 10v+
J38: USB; uUSB_new; Part Number 10103594-0001LF
J39: uSD_Socket; uSD_SKT; Part Number 693071020811
J40: SHIELD_GND; 2.8mm_Spade_terminal; Part Number DNP - PC110D5
J41: Ethernet; RJ45+MAG; Part Number HR911105A
L8, L9: 1K @100Mhz; L_0603_1608Metric; Part Number BK1608HS102-T or PE-0603FB102ST or simi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
L30: CM Choke; Wurth_CM_Choke_744231121; Part Number 744231121 or SRF2012A-121YA
R26: 100R; R_0402_1005Metric_Wbry
R32, R114: 1M; R_0805_2012Metric; Part Number RMCF0805JT1M00
R86: 47K; R_0402_1005Metric_Wbry; Part Number RMCF0402FT47K0
R87, R88, R107: 27R; R_0402_1005Metric_Wbry; Part Number RC0402FR-0727RL
R90: 27K; R_0402_1005Metric_Wbry; Part Number RK73H1ETTP2702F
R96, R97: 59R 1%; R_0402_1005Metric_Wbry; Part Number RK73H1ETTP59R0F
R99, R103, R109, R111: 10K; R_0402_1005Metric_Wbry; Part Number RK73H1ETTP1002F
R104: 4K7; R_0402_1005Metric_Wbry; Part Number RK73H1ETTP4701F
R105: 1.5K DNP; R_0402_1005Metric_Wbry; Part Number DNP
R108: 1K; R_0402_1005Metric_Wbry; Part Number RK73H1ETTP1001F
R110: 6K49; R_0402_1005Metric_Wbry; Part Number RC0402FR-076K49L
R112, R113: 470R; R_0402_1005Metric_Wbry; Part Number RK73H1ETTP4700F
U19: KSZ8081RNACA; KSZ8081RNA _QFN-24-1EP_4x4mm_P0.5mm_EP2.6x2.6mm; Part Number KSZ8081RNACA
U20: CM1624; UDFN-16-1EP_1.35x3.3_P0.4_Duet3D; Part Number CM1624−08DE
U21: MCP2542; DFN-8-1EP_3x2mm_P0.5mm_EP1.3x1.5mm; Part Number MCP2542FDT-E/MNY
U22: TPD4S012; USON-6_1.45x1_TI_DRY06mm; Part Number TPD4S012DRYR

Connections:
5V_INT: C95.1, U21.3 (VDD); also elsewhere on the board
+3.3V: C26.1, C127.1, J39.4 (VDD), L8.1 (A), L9.1 (A), R99.2, R105.1, R108.1, R111.1, R112.1, U20.12 (VCC), U21.5 (VIO); also elsewhere on the board
/Comms/CANH_C: L30.1, U21.7 (CANH)
/Comms/CANL_C: L30.4, U21.6 (CANL)
/Comms/CE: C128.2, J38.CE, R32.2
/Comms/CLK: J39.5 (CLK), U20.14 (CLK)
/Comms/CMD: J39.3 (CMD), U20.11 (CMD)
/Comms/DAT0: J39.7 (DAT0/DO), U20.10 (Data3)
/Comms/DAT1: J39.8 (DAT1), U20.9 (Data2)
/Comms/DAT2: J39.1 (DAT2), U20.16 (Data1)
/Comms/DAT3: J39.2 (DAT3), U20.15 (Data0)
/Comms/LED0: J41.10 (LEDG_K), R111.2, U19.23 (LED0)
/Comms/RCT: C139.1, J41.5 (RCT)
/Comms/RD+: J41.3 (RD+), U19.4 (RXP)
/Comms/RD-: J41.6 (RD-), U19.3 (RXM)
/Comms/REXT: R110.1, U19.9 (REXT)
/Comms/SD_cd: J39.9 (Card_Detect), R99.1, U20.13 (ESD1)
/Comms/SHIELD_GND: C140.2, J40.1, J41.8 (GND), J41.13 (SHIELD), J41.14 (SHIELD), R114.2
/Comms/TCT: C138.1, J41.4 (TCT)
/Comms/TD+: J41.1 (TD+), U19.6 (TXP)
/Comms/TD-: J41.2 (TD-), U19.5 (TXM)
/Comms/VDDA_3V3: C131.1, C132.1, L8.2 (B), U19.2 (VDDA_3V3)
/Comms/VDDIO: C135.1, C136.1, L9.2 (B), U19.14 (VDDIO)
/Comms/VDD_1V2: C133.1, C134.1, U19.1 (VDD_1V2)
/Comms/XI: R26.1, U19.8 (XI)
/Comms/dn: J38.2 (DN), R88.1, U22.1 (D+)
/Comms/dp: J38.3 (DP), R87.1, U22.2 (D-)
/Comms/refclk: R107.2, U19.16 (REF_CLK)
CAN1_RX: U21.4 (RXD); also elsewhere on the board
CAN1_TX: U21.1 (TXD); also elsewhere on the board
CAN_H: L30.2, R96.1; also elsewhere on the board
CAN_L: L30.3, R97.2; also elsewhere on the board
CLK_OUT: R26.2; also elsewhere on the board
CRSDV: R109.1, U19.15 (CRS_RV); also elsewhere on the board
GMDC: R105.2, U19.11 (MDC); also elsewhere on the board
GMDIO: R108.2, U19.10 (MDIO); also elsewhere on the board
GND: C26.2, C95.2, C97.1, C126.2, C127.2, C128.1, C131.2, C132.2, C133.2, C134.2, C135.2, C136.2, C138.2, C139.2, C140.1, J38.5 (GND), J39.6 (GND), J39.G (GND), R32.1, R86.2, R103.2, R104.2, R109.2, R110.2, R113.2, R114.1, U19.22 (GND1), U19.25 (GND2), U20.PAD (GND), U21.2 (VSS), U21.8 (S), U21.9 (PAD), U22.4 (GND); also elsewhere on the board
GRX0: U19.13 (RXD0); also elsewhere on the board
GRX1: U19.12 (RXD1); also elsewhere on the board
GRXER: R103.1, U19.17 (RXER); also elsewhere on the board
GTX0: U19.20 (TXD0); also elsewhere on the board
GTX1: U19.21 (TXD1); also elsewhere on the board
GTXEN: U19.19 (TXEN); also elsewhere on the board
unnamed: C97.2, R96.2, R97.1
unnamed: J41.9 (LEDG_A), R112.2
unnamed: J41.11 (LEDY_K), R113.1
PHY_RST: J41.12 (LEDY_A), R104.1, U19.24 (~RST); also elsewhere on the board
REF_CLK: R107.1; also elsewhere on the board
SDCK: U20.3 (SDClk); also elsewhere on the board
SDCMD: U20.6 (SDCMD); also elsewhere on the board
SD_CD: U20.4 (ESD1); also elsewhere on the board
SD_DAT0: U20.7 (SDData3); also elsewhere on the board
SD_DAT1: U20.8 (SDData2); also elsewhere on the board
SD_DAT2: U20.1 (SDData1); also elsewhere on the board
SD_DAT3: U20.2 (SDData0); also elsewhere on the board
USB_D_N: R88.2; also elsewhere on the board
USB_D_P: R87.2; also elsewhere on the board
VBUS: J38.1 (VBUS), R90.1, U22.6 (VBUS); also elsewhere on the board
VBUS_DETECT: C126.1, R86.1, R90.2; also elsewhere on the board

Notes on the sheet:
USB
ESD protection shield ground point
Ethernet
Values of L10, L12 TBD Not specified
uSD
10K pullup on pin 15 is probably not required (PHY address select, the default is fine).
CAN Transceiver

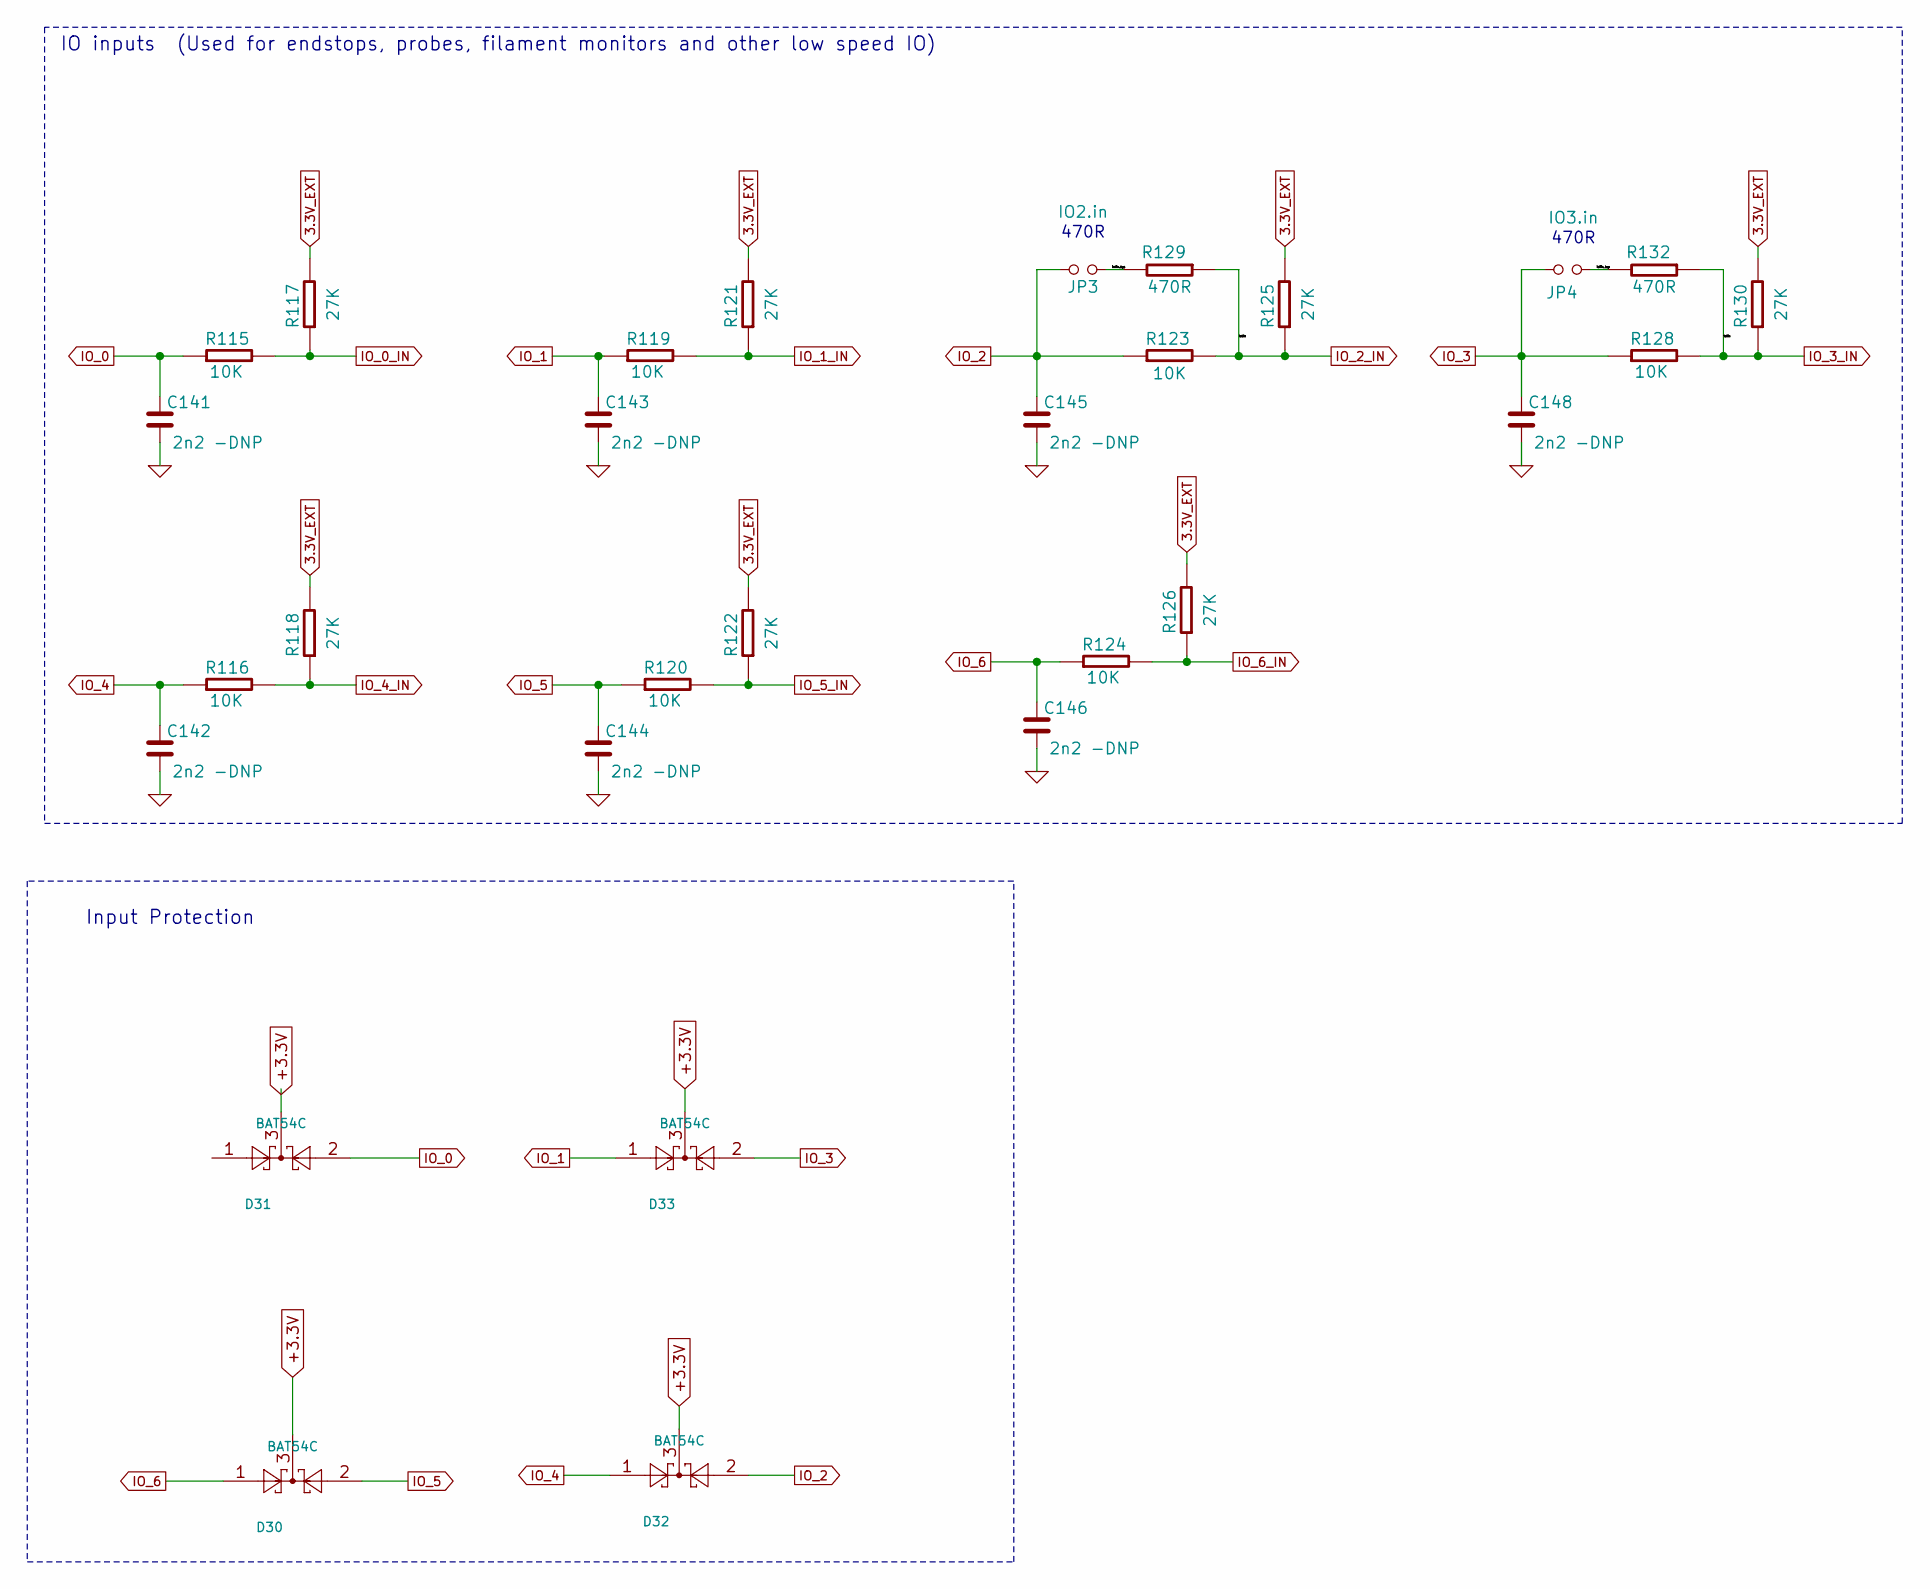
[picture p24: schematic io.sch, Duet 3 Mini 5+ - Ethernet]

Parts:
C141, C142, C143, C144, C145, C146, C148: 2n2 -DNP; C_0402_1005Metric_Wbry; Part Number DNP
D30, D31, D32, D33: BAT54C; SOT-23; Part Number BAT54C-7-F
JP3: IO2.in; PinHeader_1x02_P2.54mm_Vertical; Part Number THS-02-R
JP4: IO3.in; PinHeader_1x02_P2.54mm_Vertical; Part Number THS-02-R
R115, R116, R119, R120, R123, R124, R128: 10K; R_0402_1005Metric_Wbry; Part Number RK73H1ETTP1002F
R117, R118, R121, R122, R125, R126, R130: 27K; R_0402_1005Metric_Wbry; Part Number RK73H1ETTP2702F
R129, R132: 470R; R_0402_1005Metric_Wbry; Part Number RK73H1ETTP4700F

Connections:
3.3V_EXT: R117.2, R118.2, R121.2, R122.2, R125.2, R126.2, R130.2; also elsewhere on the board
+3.3V: D30.3, D31.3, D32.3, D33.3; also elsewhere on the board
/IO/io2in_byp: JP3.2, R129.2
/IO/io3in_byp: JP4.2, R132.2
GND: C141.2, C142.2, C143.2, C144.2, C145.2, C146.2, C148.2; also elsewhere on the board
IO_0: C141.1, D31.2, R115.1; also elsewhere on the board
IO_0_IN: R115.2, R117.1; also elsewhere on the board
IO_1: C143.1, D33.1, R119.1; also elsewhere on the board
IO_1_IN: R119.2, R121.1; also elsewhere on the board
IO_2: C145.1, D32.2, JP3.1, R123.1; also elsewhere on the board
IO_2_IN: R123.2, R125.1, R129.1; also elsewhere on the board
IO_3: C148.1, D33.2, JP4.1, R128.1; also elsewhere on the board
IO_3_IN: R128.2, R130.1, R132.1; also elsewhere on the board
IO_4: C142.1, D32.1, R116.1; also elsewhere on the board
IO_4_IN: R116.2, R118.1; also elsewhere on the board
IO_5: C144.1, D30.2, R120.1; also elsewhere on the board
IO_5_IN: R120.2, R122.1; also elsewhere on the board
IO_6: C146.1, D30.1, R124.1; also elsewhere on the board
IO_6_IN: R124.2, R126.1; also elsewhere on the board

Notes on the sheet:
IO inputs (Used for endstops, probes, filament monitors and other low speed IO)
Input Protection
470R

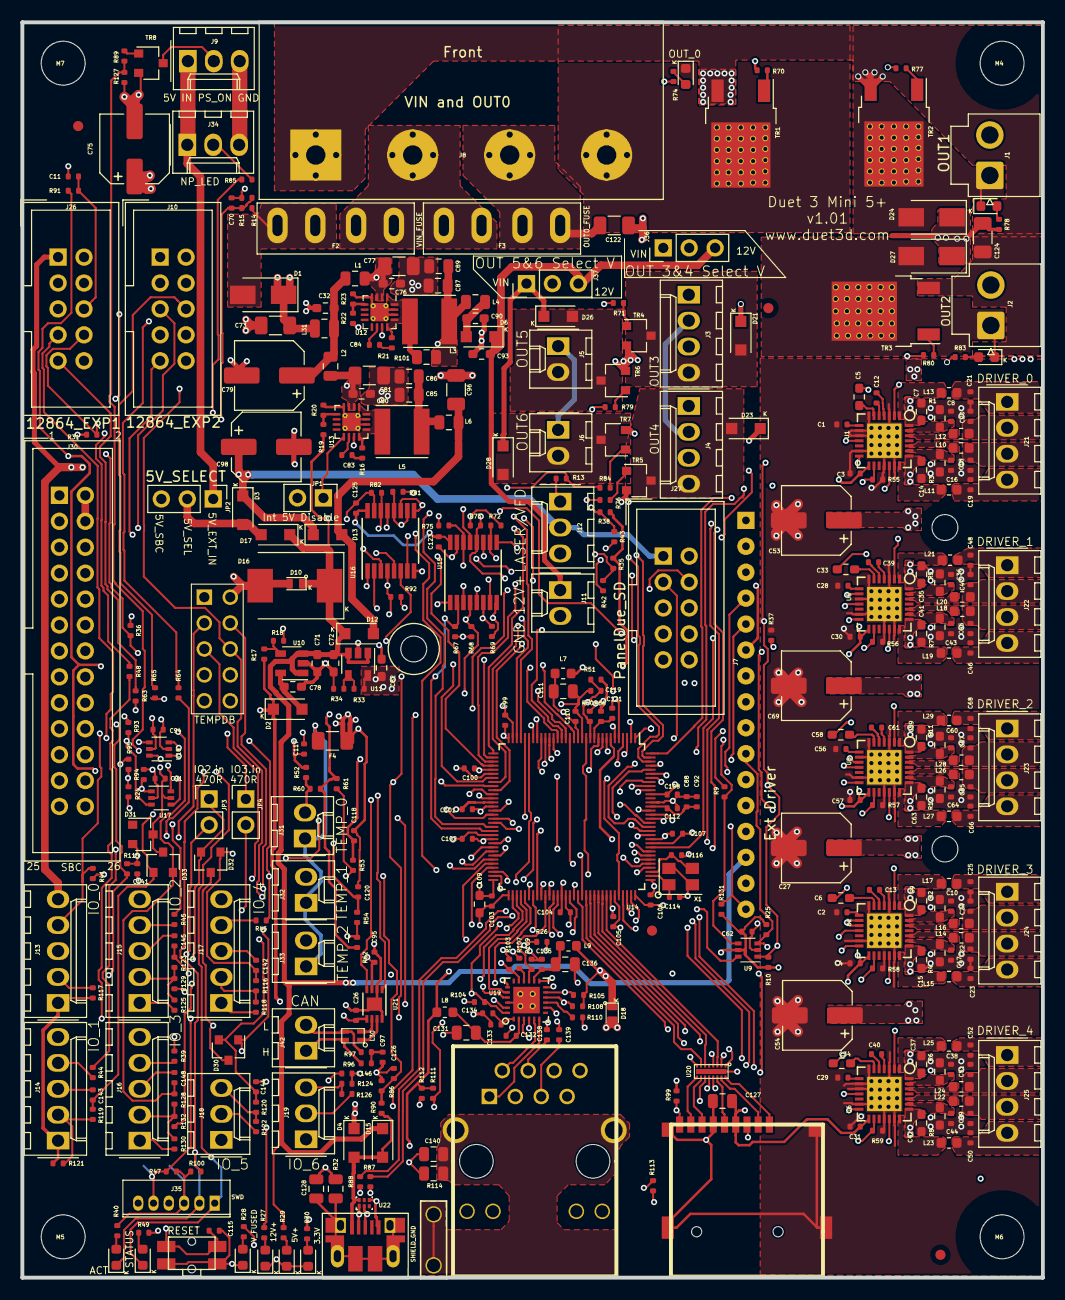
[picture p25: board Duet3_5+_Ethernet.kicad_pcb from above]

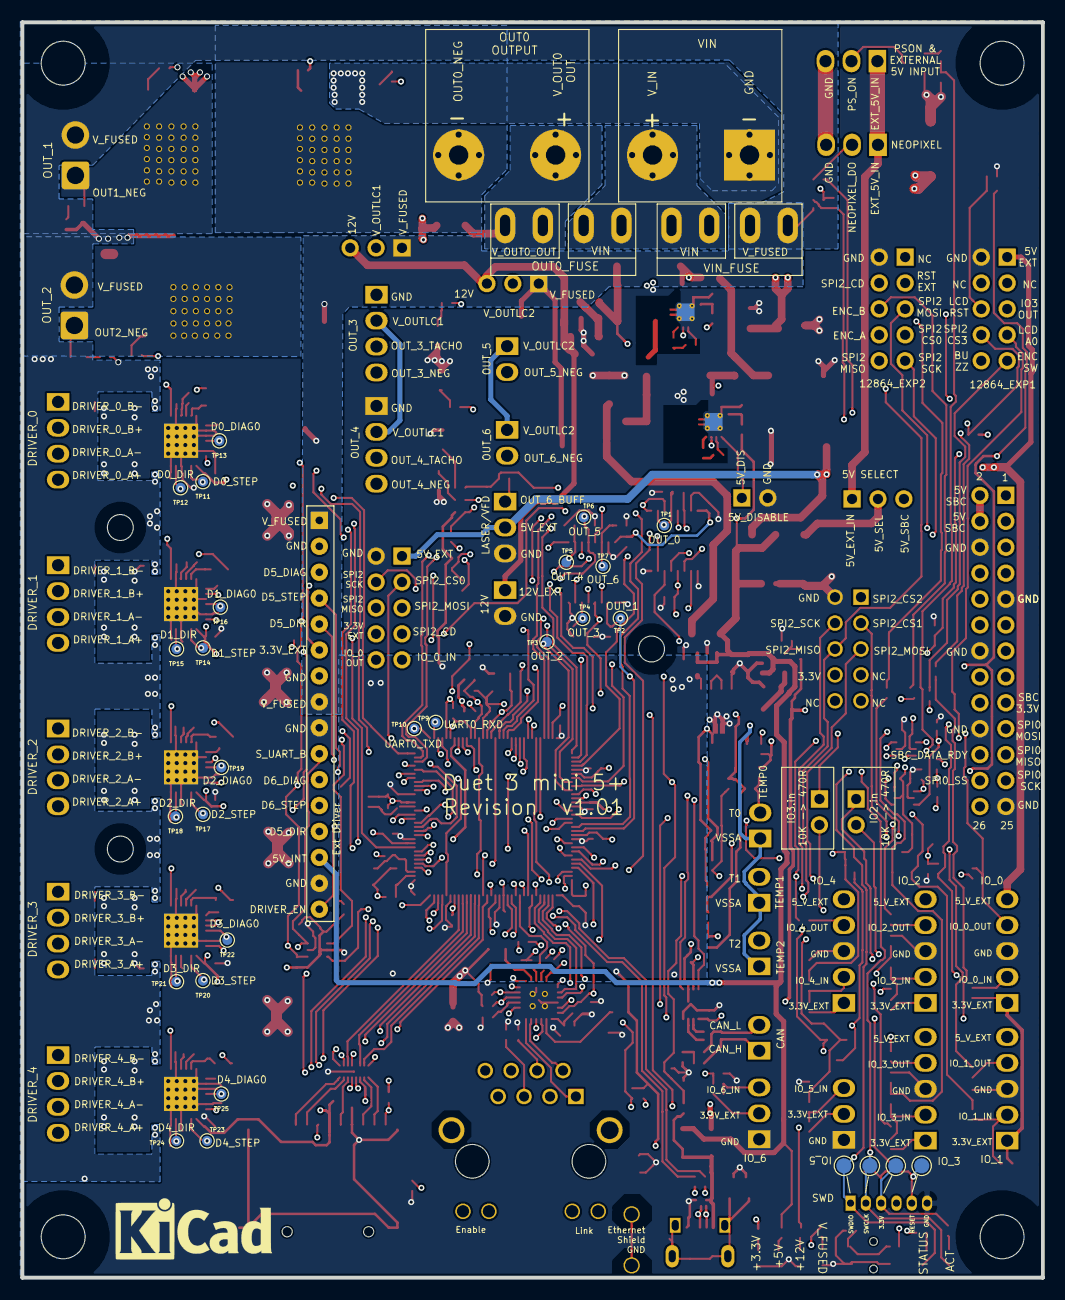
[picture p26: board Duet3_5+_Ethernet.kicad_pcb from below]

Board: 4 copper layers, 100.0 x 123.0 mm, 447 parts (29 on the bottom side), 310 nets.

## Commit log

2021-05-04 Add STEPs files and Schematics
2021-08-02 Mini 5+ v1.01 Schematics and STEP files
2021-08-05 Added Mini 2+ Schematic & Step File
    [Duet3_Exp_2plus.step]
2022-03-31 Mini 5+ v1.01 KiCAD files
    [Comms.sch, Duet3_5+_Ethernet.kicad_pcb, Duet3_5+_Ethernet.sch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]
